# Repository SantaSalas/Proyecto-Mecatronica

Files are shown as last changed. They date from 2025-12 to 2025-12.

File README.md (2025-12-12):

<h1> Robot balancín, ¡Bienvenidos al Himalaya! </h1>

## Curso
- ME4250
## Integrantes
- Consuelo Laurie
- Martín Batarce
- Santiago Salas
- Benjamín Venegas
- Francisca Suárez
## Lista de materiales 
1. 2 Motor DC
2. 2 Ruedas
3. 3 Baterias 4V
4. 1 MPU6050
5. 1 Motor driver L298N
6. 1 Placa Arduino Uno
7. 12 Pernos M3
8. 12 Tuercas M3
9. 4 Escuadras rectangulares
10. 1 Techo CAD
11. 2 Paredes CAD
12. 1 Piso 1 CAD
13. 1 Piso 2 CAD
14. 1 Base CAD
15. 18 Cables macho-macho
16. Pegamento líquido UHU
17. Carcasa Bienvenidos al Himalaya (edición limitada)
18. 1 Switch encendido/apagado
19. 1 Portapilas
20. Cinta doble faz
21. Cinta masking tape
## Diagrama de conexiones electrónicas.
IMG-20251212-WA0009

## Manual de armado 
1. Armado Chasis: Una vez impresas todas paredes y ruedas de PLA en impresora 3d, se pegan con pegamento UHU las 4 paredes exteriores. Luego pegar escuadras metálicas cercanas a las esquinas.
*Procurar la correcta orientación de las paredes al momento de pegarlas.
2. Instalación motores: En las paredes laterales instalar ambos motores DC con pernos y tuercas M3 en los agujeros existentes. Luego con pegamento UHU, pegar las ruedas a los ejes de los motores, una rueda en cada motor.
3. Armado Piso 1: Instalar Motor driver L298N y Arduino con pernos y tuercas M3 en los agujeros existentes. Pegar Portapilas en la parte inferior del piso afirmado con cinta doble faz y cinta masking tape, se instala cercano al borde delantero y procurando que esté centrado. Luego instalar pilas y pegar al portapilas el switch de encendido/apagado con cinta doble faz.
4. Armado Piso 2: Instalar MPU6050 con pernos y tuercas M3 en los agujeros existentes.
5. Cableado: Ya instalados los componentes, seguir el diagrama de conexiones para realizar las conexiones eléctricas, utilizando los cables macho-macho.
6. Montaje: Los pisos se instalan sobre los descansos de las paredes y reforzando con pegamento UHU. Finalmente colocar la carcasa, preocurando que ningún cable que apretado entre la carcasa y la estructura.

## Puesta en marcha
1. Subir el código Arduino listo para utilizar el Robot Balancín.
2. Levantar el robot y colocar únicamente la base del robot en una superficie lisa y plana (puede ser una caja).
3. Encender el robot y esperar 3 segundos a que termine el proceso de calibración.
4. Dejar el robot libre sobre una superficie plana para que comience a balancearse.
5. En caso de falla levantar el robot por la carcasa y apagar el switch, no agarrarlo desde las ruedas.

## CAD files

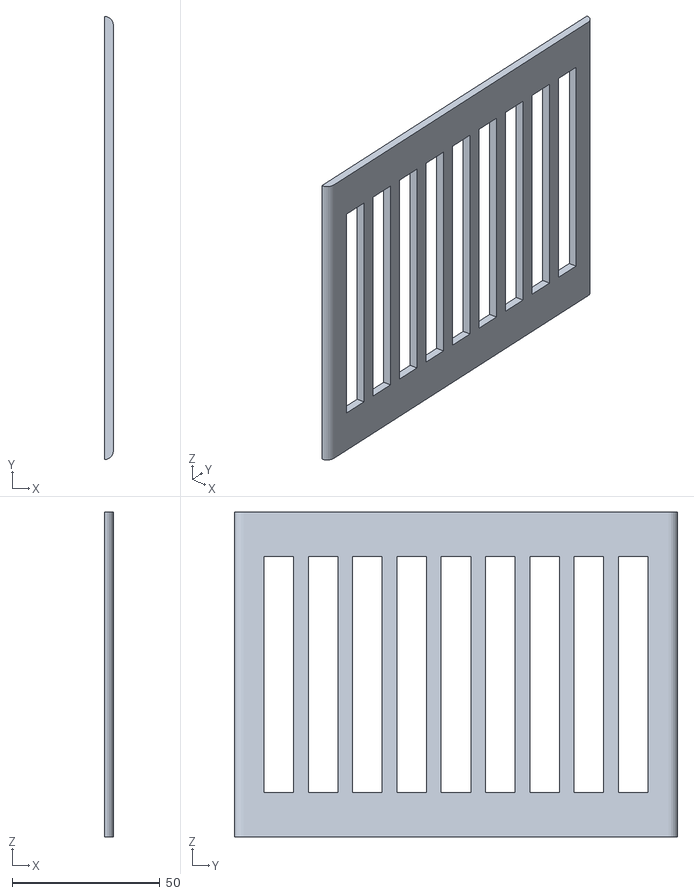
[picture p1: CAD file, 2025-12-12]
Robot Autobalacin/CAD/Techo.stl
3.00 x 150.0 x 110.0

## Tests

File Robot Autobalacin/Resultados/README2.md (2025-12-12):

## Audiovisual

WhatsApp-Image-2025-11-10-at-15 03 37-_4_
WhatsApp-Image-2025-11-10-at-15 03 37-_5_

https://github.com/user-attachments/assets/5a2925b6-6c78-46cb-873b-391fbea81871

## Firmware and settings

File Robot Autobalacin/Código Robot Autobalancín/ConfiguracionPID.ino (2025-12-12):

/*
  ROBOT AUTO-BALANCÍN - CONTROL PID COMPLETO
  ME4250 - Mecatrónica - Universidad de Chile
  Basado en estructura PID de muestra del curso
  
  Hardware: Arduino UNO + MPU6050 + L298N + 2x Motor DC
*/

#include <Wire.h>

//////////////////// CONFIGURACIÓN HARDWARE ////////////////////
// Pines MPU6050 (I2C)
const int MPU6050_ADDR = 0x68;  // Dirección I2C
// SDA -> A4, SCL -> A5 (hardware I2C)

// Pines Motor Izquierdo
const int ENA_IZQ = 5;     // PWM motor izquierdo
const int IN1_IZQ = 7;      // Control dirección
const int IN2_IZQ = 6;      // Control dirección

// Pines Motor Derecho  
const int ENB_DER = 11;     // PWM motor derecho
const int IN3_DER = 4;      // Control dirección
const int IN4_DER = 3;      // Control dirección

// Límites de seguridad
const float ANGULO_MAX = 35.0;      // [AJUSTAR] Ángulo límite seguridad
const int PWM_MIN = 50;             // [AJUSTAR] PWM mínimo efectivo
const int PWM_MAX = 255;            // PWM máximo
const int ZONA_MUERTA = 40;         // [AJUSTAR] Zona donde motores no responden

//////////////////// PARÁMETROS PID ////////////////////////////
// [AJUSTAR] Valores iniciales conservadores
float Kp = 20.0;   // Ganancia proporcional
float Ki = 0.5;    // Ganancia integral  
float Kd = 10.0;   // Ganancia derivativa
float setpoint = 0.0;  // [AJUSTAR] Ángulo objetivo (0 = vertical)

//////////////////// VARIABLES DEL CONTROL /////////////////////
float angulo = 0.0;           // Ángulo actual del robot
float error = 0.0;            // Error actual
float error_prev = 0.0;       // Error anterior
float integral = 0.0;         // Acumulador integral
float derivada = 0.0;         // Componente derivativa
float salida = 0.0;           // Salida del PID
int pwm_izq = 0;              // PWM motor izquierdo
int pwm_der = 0;              // PWM motor derecho

// Variables componentes PID (para análisis)
float P_term = 0.0;
float I_term = 0.0;
float D_term = 0.0;

// Control de tiempo
unsigned long lastTime = 0;
const unsigned long sampleTime = 10;  // [AJUSTAR] ms (100 Hz)

//////////////////// VARIABLES SENSOR MPU6050 //////////////////
// Datos crudos
int16_t accelX, accelY, accelZ;
int16_t gyroX, gyroY, gyroZ;
int16_t temperatura;

// Offsets calibración
float accelX_offset = 0;
float accelY_offset = 0;
float gyroY_offset = 0;

// Filtro complementario
const float ALPHA = 0.98;  // [AJUSTAR] 98% gyro, 2% accel

// Estado del sistema
bool sistemaCalibrado = false;
bool controlActivo = false;
bool emergencyStop = false;

//////////////////// VARIABLES ANÁLISIS MÉTRICAS ///////////////
float anguloMaximo = 0.0;     // Para calcular overshoot
float tiempoEstablecido = 0.0;  // Tiempo establecimiento
unsigned long tiempoInicio = 0;
bool primeraVez = true;
float sumaError = 0.0;         // Para error estacionario
int contadorError = 0;

//////////////////// FUNCIONES AUXILIARES - MOTORES ////////////
void configurarMotores() {
  pinMode(ENA_IZQ, OUTPUT);
  pinMode(IN1_IZQ, OUTPUT);
  pinMode(IN2_IZQ, OUTPUT);
  
  pinMode(ENB_DER, OUTPUT);
  pinMode(IN3_DER, OUTPUT);
  pinMode(IN4_DER, OUTPUT);
  
  detenerMotores();
  Serial.println("[MOTORES] Configurados OK");
}

void moverMotores(int pwmValue) {
  // Aplicar zona muerta
  if (abs(pwmValue) < ZONA_MUERTA) {
    detenerMotores();
    return;
  }
  
  // Mapear considerando zona muerta
  int pwmAjustado = abs(pwmValue);
  if (pwmAjustado > ZONA_MUERTA) {
    pwmAjustado = map(pwmAjustado, ZONA_MUERTA, PWM_MAX, PWM_MIN, PWM_MAX);
  }
  
  pwmAjustado = constrain(pwmAjustado, 0, PWM_MAX);
  
  if (pwmValue > 0) {
    // Mover adelante
    digitalWrite(IN1_IZQ, HIGH);
    digitalWrite(IN2_IZQ, LOW);
    analogWrite(ENA_IZQ, pwmAjustado);
    
    digitalWrite(IN3_DER, HIGH);
    digitalWrite(IN4_DER, LOW);
    analogWrite(ENB_DER, pwmAjustado);
    
  } else {
    // Mover atrás
    digitalWrite(IN1_IZQ, LOW);
    digitalWrite(IN2_IZQ, HIGH);
    analogWrite(ENA_IZQ, pwmAjustado);
    
    digitalWrite(IN3_DER, LOW);
    digitalWrite(IN4_DER, HIGH);
    analogWrite(ENB_DER, pwmAjustado);
  }
}

void detenerMotores() {
  digitalWrite(IN1_IZQ, LOW);
  digitalWrite(IN2_IZQ, LOW);
  analogWrite(ENA_IZQ, 0);
  
  digitalWrite(IN3_DER, LOW);
  digitalWrite(IN4_DER, LOW);
  analogWrite(ENB_DER, 0);
}

//////////////////// FUNCIONES AUXILIARES - MPU6050 ////////////
void configurarMPU6050() {
  Wire.begin();
  
  // Despertar MPU6050
  Wire.beginTransmission(MPU6050_ADDR);
  Wire.write(0x6B);  // PWR_MGMT_1
  Wire.write(0);     // Despertar
  Wire.endTransmission(true);
  
  delay(100);
  
  // Verificar comunicación
  Wire.beginTransmission(MPU6050_ADDR);
  if (Wire.endTransmission() == 0) {
    Serial.println("[MPU6050] Detectado OK");
  } else {
    Serial.println("[ERROR] MPU6050 no detectado!");
    emergencyStop = true;
  }
}

void leerMPU6050Raw() {
  Wire.beginTransmission(MPU6050_ADDR);
  Wire.write(0x3B);  // ACCEL_XOUT_H
  Wire.endTransmission(false);
  Wire.requestFrom(MPU6050_ADDR, 14, true);
  
  accelX = Wire.read() << 8 | Wire.read();
  accelY = Wire.read() << 8 | Wire.read();
  accelZ = Wire.read() << 8 | Wire.read();
  temperatura = Wire.read() << 8 | Wire.read();
  gyroX = Wire.read() << 8 | Wire.read();
  gyroY = Wire.read() << 8 | Wire.read();
  gyroZ = Wire.read() << 8 | Wire.read();
}

float calcularAngulo(float dt) {
  // Ángulo desde acelerómetro
  float accelAngulo = atan2(accelX - accelX_offset, accelZ) * 180 / PI;
  
  // Velocidad angular desde giroscopio
  float gyroRate = (gyroY / 131.0) - gyroY_offset;
  
  // Filtro complementario
  angulo = ALPHA * (angulo + gyroRate * dt) + (1 - ALPHA) * accelAngulo;
  
  return angulo;
}

void calibrarSensor() {
  Serial.println("\n[CALIBRACIÓN] Mantener robot VERTICAL y QUIETO");
  Serial.print("Calibrando");
  
  // Reset valores
  accelX_offset = 0;
  accelY_offset = 0;
  gyroY_offset = 0;
  angulo = 0;
  
  // Tomar muestras
  const int numMuestras = 200;
  long sumaAX = 0, sumaAY = 0, sumaGX = 0;
  
  for (int i = 0; i < numMuestras; i++) {
    leerMPU6050Raw();
    sumaAX += accelX;
    sumaAY += accelY;
    sumaGX += gyroX;
    
    if (i % 40 == 0) Serial.print(".");
    delay(5);
  }
  
  // Calcular offsets
  accelX_offset = sumaAX / numMuestras;
  accelY_offset = sumaAY / numMuestras;
  gyroX_offset = (sumaGX / numMuestras) / 131.0;
  
  Serial.println("\n[CALIBRACIÓN] Completada!");
  Serial.print("  Offset Gyro X: ");
  Serial.println(gyroX_offset);
  
  sistemaCalibrado = true;
  tiempoInicio = millis();
  primeraVez = true;
}

//////////////////// FUNCIÓN ANÁLISIS MÉTRICAS /////////////////
void analizarMetricas() {
  // Detectar overshoot
  if (abs(angulo) > abs(anguloMaximo)) {
    anguloMaximo = angulo;
  }
  
  // Acumular error para estacionario
  if (!primeraVez && abs(error) < 2.0) {  // Banda 2%
    sumaError += abs(error);
    contadorError++;
  }
  
  // Detectar establecimiento (criterio 2%)
  if (primeraVez && abs(error) < 1.0) {
    tiempoEstablecido = (millis() - tiempoInicio) / 1000.0;
    primeraVez = false;
    
    // Mostrar métricas
    float overshoot = abs(anguloMaximo) > abs(setpoint) ? 
                      ((anguloMaximo - setpoint) / max(abs(setpoint), 1.0)) * 100 : 0;
    
    Serial.println("\n========== MÉTRICAS PID ==========");
    Serial.print("Ts (establecimiento): ");
    Serial.print(tiempoEstablecido, 2);
    Serial.println(" seg");
    Serial.print("%OS (overshoot): ");
    Serial.print(overshoot, 1);
    Serial.println("%");
    Serial.println("==================================");
  }
}

//////////////////// SETUP //////////////////////
void setup() {
  Serial.begin(115200);
  
  Serial.println("\n  ROBOT AUTO-BALANCÍN PID V3   ");
  
  configurarMotores();
  configurarMPU6050();
  
  Serial.println("\nCOMANDOS DISPONIBLES:");
  Serial.println("  C = Calibrar sensor");
  Serial.println("  P = Iniciar control PID");
  Serial.println("  S = STOP emergencia");
  Serial.println("  + = Aumentar setpoint");
  Serial.println("  - = Reducir setpoint");
  Serial.println("  R = Reporte estado");
  Serial.println("  T = Tuning (ajuste Kp,Ki,Kd)");
  Serial.println("\nEsperando comando...\n");
  
  lastTime = millis();
}

//////////////////// LOOP PRINCIPAL //////////////////////
void loop() {
  // Procesar comandos serial
  if (Serial.available()) {
    procesarComandos();
  }
  
  // Control de emergencia
  if (emergencyStop) {
    detenerMotores();
    return;
  }
  
  // Control PID con tiempo de muestreo
  unsigned long now = millis();
  if ((now - lastTime >= sampleTime) && controlActivo && sistemaCalibrado) {
    float dt = (now - lastTime) / 1000.0;  // Convertir a segundos
    lastTime = now;
    
    // 1) Leer sensor y calcular ángulo
    leerMPU6050Raw();
    angulo = calcularAngulo(dt);
    
    // 2) Verificación de seguridad
    if (abs(angulo) > ANGULO_MAX) {
      emergencyStop = true;
      detenerMotores();
      Serial.println("[EMERGENCIA] Ángulo límite excedido!");
      return;
    }
    
    // 3) Calcular error
    error = setpoint - angulo;
    
    // 4) PID (cálculo manual como el ejemplo)
    P_term = Kp * error;
    
    integral += error * dt;
    I_term = Ki * integral;
    
    derivada = (error - error_prev) / dt;
    D_term = Kd * derivada;
    
    salida = P_term + I_term + D_term;
    
    // 5) Anti-windup (como el ejemplo)
    if (salida > PWM_MAX) {
      salida = PWM_MAX;
      integral -= error * dt;  // Evita acumulación excesiva
    } else if (salida < -PWM_MAX) {
      salida = -PWM_MAX;
      integral -= error * dt;
    }
    
    // 6) Limitar integral independientemente
    integral = constrain(integral, -100, 100);
    
    // 7) Convertir a PWM
    int pwm = (int)salida;
    
    // 8) Aplicar a motores
    moverMotores(pwm);
    
    // 9) Mostrar datos para Serial Plotter
    // Formato: angulo,setpoint,pwm,P,I,D
    Serial.print(angulo);
    Serial.print(",");
    Serial.print(setpoint);
    Serial.print(",");
    Serial.print(pwm/10.0);  // Escalar PWM para visualización
    Serial.print(",");
    Serial.print(P_term);
    Serial.print(",");
    Serial.print(I_term);
    Serial.print(",");
    Serial.println(D_term);
    
    // 10) Analizar métricas
    analizarMetricas();
    
    // 11) Guardar error anterior
    error_prev = error;
    
    // 12) Reporte error estacionario cada 2 segundos
    static unsigned long lastReport = 0;
    if (now - lastReport > 2000 && contadorError > 0) {
      float errorProm = sumaError / contadorError;
      if (errorProm < 2.0 && !primeraVez) {
        Serial.print("[ESTACIONARIO] Error promedio: ");
        Serial.print(errorProm, 2);
        Serial.println("°");
      }
      lastReport = now;
    }
  }
}

//////////////////// PROCESAMIENTO DE COMANDOS /////////////////
void procesarComandos() {
  char cmd = Serial.read();
  
  switch(cmd) {
    case 'C':
    case 'c':
      calibrarSensor();
      break;
      
    case 'P':
    case 'p':
      if (sistemaCalibrado) {
        controlActivo = true;
        emergencyStop = false;
        integral = 0;  // Reset integral
        error_prev = 0;
        Serial.println("[CONTROL] PID activado");
      } else {
        Serial.println("[ERROR] Calibrar primero con 'C'");
      }
      break;
      
    case 'S':
    case 's':
      emergencyStop = !emergencyStop;
      controlActivo = false;
      detenerMotores();
      if (emergencyStop) {
        Serial.println("[STOP] Emergencia activada");
      } else {
        Serial.println("[STOP] Sistema listo");
      }
      break;
      
    case '+':
      setpoint += 1.0;
      Serial.print("[SETPOINT] Nuevo: ");
      Serial.print(setpoint);
      Serial.println("°");
      break;
      
    case '-':
      setpoint -= 1.0;
      Serial.print("[SETPOINT] Nuevo: ");
      Serial.print(setpoint);
      Serial.println("°");
      break;
      
    case 'R':
    case 'r':
      Serial.println("\n===== ESTADO ACTUAL =====");
      Serial.print("Ángulo: ");
      Serial.print(angulo, 2);
      Serial.println("°");
      Serial.print("Setpoint: ");
      Serial.print(setpoint, 2);
      Serial.println("°");
      Serial.print("Error: ");
      Serial.print(error, 2);
      Serial.println("°");
      Serial.print("Kp: ");
      Serial.print(Kp);
      Serial.print(" | Ki: ");
      Serial.print(Ki);
      Serial.print(" | Kd: ");
      Serial.println(Kd);
      Serial.print("Calibrado: ");
      Serial.println(sistemaCalibrado ? "SI" : "NO");
      Serial.print("Control activo: ");
      Serial.println(controlActivo ? "SI" : "NO");
      Serial.println("========================");
      break;
      
    case 'T':
    case 't':
      menuTuning();
      break;
      
    case '?':
      Serial.println("\n=== AYUDA COMANDOS ===");
      Serial.println("C = Calibrar (hacer primero)");
      Serial.println("P = Activar PID");
      Serial.println("S = Stop/Resume");
      Serial.println("+/- = Ajustar setpoint");
      Serial.println("R = Reporte estado");
      Serial.println("T = Tuning PID");
      Serial.println("======================");
      break;
  }
}

//////////////////// MENÚ TUNING INTERACTIVO //////////////////
void menuTuning() {
  Serial.println("\n=== TUNING PID ===");
  Serial.println("Valores actuales:");
  Serial.print("  Kp=");
  Serial.print(Kp);
  Serial.print(" Ki=");
  Serial.print(Ki);
  Serial.print(" Kd=");
  Serial.println(Kd);
  
  Serial.println("\nIngrese nuevos valores:");
  Serial.println("Formato: P20.5 (para Kp=20.5)");
  Serial.println("         I0.8  (para Ki=0.8)");
  Serial.println("         D12.0 (para Kd=12.0)");
  Serial.println("         X     (salir)");
  
  while(true) {
    if (Serial.available()) {
      char tipo = Serial.read();
      if (tipo == 'X' || tipo == 'x') {
        Serial.println("Tuning finalizado");
        break;
      }
      
      float valor = Serial.parseFloat();
      
      switch(tipo) {
        case 'P':
        case 'p':
          Kp = valor;
          Serial.print("Nuevo Kp = ");
          Serial.println(Kp);
          break;
          
        case 'I':
        case 'i':
          Ki = valor;
          integral = 0;  // Reset integral al cambiar Ki
          Serial.print("Nuevo Ki = ");
          Serial.println(Ki);
          break;
          
        case 'D':
        case 'd':
          Kd = valor;
          Serial.print("Nuevo Kd = ");
          Serial.println(Kd);
          break;
      }
    }
  }
  
  Serial.println("\nValores finales:");
  Serial.print("  Kp=");
  Serial.print(Kp);
  Serial.print(" Ki=");
  Serial.print(Ki);
  Serial.print(" Kd=");
  Serial.println(Kd);
}

/*
  =====================================================
  GUÍA RÁPIDA DE AJUSTE PID - MÉTODO ZIEGLER-NICHOLS
  =====================================================
  
  1. AJUSTE INICIAL (Solo P):
     - Poner Ki=0, Kd=0
     - Aumentar Kp hasta oscilación sostenida
     - Anotar: Kp_critico y T_critico (periodo)
  
  2. CÁLCULO PID:
     - Kp = 0.6 * Kp_critico
     - Ki = 2 * Kp / T_critico
     - Kd = Kp * T_critico / 8
  
  3. AJUSTE FINO:
     - Si oscila: reducir Kp, aumentar Kd
     - Si lento: aumentar Kp
     - Si error permanente: aumentar Ki
  
  =====================================================
  VALORES TÍPICOS PARA ROBOT BALANCÍN
  =====================================================
  
  Robot ligero (<500g):
    Kp: 15-25
    Ki: 0.5-1.5
    Kd: 8-12
    
  Robot pesado (>500g):
    Kp: 25-40
    Ki: 1.0-2.5
    Kd: 12-20
  
  =====================================================
  SERIAL PLOTTER
  =====================================================
  
  Abrir Tools -> Serial Plotter (115200 baud)
  Se mostrarán 6 señales:
  1. Ángulo (azul)
  2. Setpoint (rojo)
  3. PWM/10 (verde)
  4. Término P (amarillo)
  5. Término I (cyan)
  6. Término D (magenta)
  
  =====================================================
*/

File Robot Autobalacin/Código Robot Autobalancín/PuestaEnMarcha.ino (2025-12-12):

#include <Wire.h>

//////////////////// CONFIGURACIÓN HARDWARE ////////////////////
const int MPU6050_ADDR = 0x68;
const int ENA = 5;         // PWM motor izquierdo
const int IN1 = 7;         // Motor izquierdo dirección
const int IN2 = 6;         // Motor izquierdo dirección  
const int ENB = 11;        // PWM motor derecho
const int IN3 = 4;         // Motor derecho dirección
const int IN4 = 3;         // Motor derecho dirección

//////////////////// PARÁMETROS PID ////////////////////////////
float Kp = 23;              // 
float Ki = 1;              // 
float Kd = 9;              // 
float setpoint = 0.0;      // Ángulo objetivo

//////////////////// PARÁMETROS SISTEMA ////////////////////////
const float ALPHA = 0.98;           // Filtro complementario
const int ZONA_MUERTA = 40;        // PWM donde motores no responden
const int PWM_MIN = 50;             // PWM mínimo efectivo
const int PWM_MAX = 255;           // PWM máximo
const float ANGULO_LIMITE = 45.0;  // Ángulo de seguridad

//////////////////// VARIABLES GLOBALES ////////////////////////
float angulo = 0.0;
float error = 0.0;
float error_prev = 0.0;
float integral = 0.0;
float derivada = 0.0;
float salida = 0.0;

unsigned long lastTime = 0;
const unsigned long sampleTime = 10;  // Control a 100Hz

int16_t accelX, accelY, accelZ;
int16_t gyroX, gyroY, gyroZ;
float gyroY_offset = 0;

bool calibrado = false;
unsigned long tiempoInicio = 0;

//////////////////// SETUP //////////////////////
void setup() {
  // Configurar pines motores
  pinMode(ENA, OUTPUT);
  pinMode(IN1, OUTPUT);
  pinMode(IN2, OUTPUT);
  pinMode(ENB, OUTPUT);
  pinMode(IN3, OUTPUT);
  pinMode(IN4, OUTPUT);
  
  // Asegurar motores detenidos
  detenerMotores();
  
  // Configurar MPU6050
  Wire.begin();
  Wire.beginTransmission(MPU6050_ADDR);
  Wire.write(0x6B);  // PWR_MGMT_1
  Wire.write(0);     // Despertar sensor
  Wire.endTransmission(true);
  
  // Esperar estabilización del sensor
  delay(500);
  
  // Calibración automática (3 segundos)
  calibrarSensor();
  
  // Inicializar tiempo
  lastTime = millis();
  tiempoInicio = millis();
}

//////////////////// LOOP PRINCIPAL //////////////////////
void loop() {
  unsigned long now = millis();
  
  // Control PID a 100Hz
  if(now - lastTime >= sampleTime) {
    float dt = (now - lastTime) / 1000.0;
    lastTime = now;
    
    // 1) Leer sensor y calcular ángulo
    leerSensor();
    calcularAngulo(dt);
    
    // 2) Verificar límite de seguridad
    if(abs(angulo) > ANGULO_LIMITE) {
      detenerMotores();
      delay(100);
      return;
    }
    
    // 3) Calcular error
    error = setpoint - angulo;
    
    // 4) Cálculo PID
    float P = Kp * error;
    
    integral += error * dt;
    float I = Ki * integral;
    
    derivada = (error - error_prev) / dt;
    float D = Kd * derivada;
    
    salida = P + I + D;
    
    // 5) Anti-windup
    if(salida > PWM_MAX) {
      salida = PWM_MAX;
      integral -= error * dt;
    } else if(salida < -PWM_MAX) {
      salida = -PWM_MAX;
      integral -= error * dt;
    }
    
    // Limitar integral
    integral = constrain(integral, -100, 100);
    
    // 6) Aplicar a motores
    int pwm = (int)salida;
    controlarMotores(pwm);
    
    // 7) Guardar error anterior
    error_prev = error;
  }
}

//////////////////// FUNCIONES AUXILIARES //////////////////////

void calibrarSensor() {
  // Calibración silenciosa (sin Serial)
  gyroY_offset = 0;
  long sumaGyroY = 0;
  long sumaAccelX = 0;
  const int numMuestras = 100;
  
  for(int i = 0; i < numMuestras; i++) {
    Wire.beginTransmission(MPU6050_ADDR);
    Wire.write(0x3B);
    Wire.endTransmission(false);
    Wire.requestFrom(MPU6050_ADDR, 14, true);
    
    accelX = Wire.read() << 8 | Wire.read();
    accelY = Wire.read() << 8 | Wire.read();
    accelZ = Wire.read() << 8 | Wire.read();
    int16_t temp = Wire.read() << 8 | Wire.read();
    gyroX = Wire.read() << 8 | Wire.read();
    gyroY = Wire.read() << 8 | Wire.read();
    gyroZ = Wire.read() << 8 | Wire.read();
    
    sumaGyroY += gyroY;
    sumaAccelX += accelX;
    
    delay(30);  // Total ~3 segundos de calibración
  }
  
  gyroY_offset = (sumaGyroY / numMuestras) / 131.0;
  
  // Calcular ángulo inicial (por si no está perfectamente horizontal)
  float accelX_prom = sumaAccelX / numMuestras;
  angulo = atan2(accelX_prom, accelZ) * 180.0 / PI;
  
  calibrado = true;
}

void leerSensor() {
  Wire.beginTransmission(MPU6050_ADDR);
  Wire.write(0x3B);
  Wire.endTransmission(false);
  Wire.requestFrom(MPU6050_ADDR, 14, true);
  
  accelX = Wire.read() << 8 | Wire.read();
  accelY = Wire.read() << 8 | Wire.read();
  accelZ = Wire.read() << 8 | Wire.read();
  int16_t temp = Wire.read() << 8 | Wire.read();
  gyroX = Wire.read() << 8 | Wire.read();
  gyroY = Wire.read() << 8 | Wire.read();
  gyroZ = Wire.read() << 8 | Wire.read();
}

void calcularAngulo(float dt) {
  // Ángulo desde acelerómetro
  float accelAngulo = -atan2(accelX, accelZ) * 180.0 / PI;
  
  // Velocidad angular desde giroscopio
  float gyroRate = (gyroY / 131.0) - gyroY_offset;
  
  // Filtro complementario
  angulo = ALPHA * (angulo + gyroRate * dt) + (1 - ALPHA) * accelAngulo;
}

void controlarMotores(int velocidad) {
  // Zona muerta
  if(abs(velocidad) < ZONA_MUERTA) {
    detenerMotores();
    return;
  }
  
  // Mapear saltando zona muerta
  int vel = abs(velocidad);
  if(vel > ZONA_MUERTA) {
    vel = map(vel, ZONA_MUERTA, PWM_MAX, PWM_MIN, PWM_MAX);
  }
  vel = constrain(vel, 0, PWM_MAX);
  
  if(velocidad > 0) {
    // Inclinado adelante -> mover adelante
    digitalWrite(IN1, HIGH);
    digitalWrite(IN2, LOW);
    analogWrite(ENA, vel);
    
    digitalWrite(IN3, HIGH);
    digitalWrite(IN4, LOW);
    analogWrite(ENB, vel);
  } else {
    // Inclinado atrás -> mover atrás
    digitalWrite(IN1, LOW);
    digitalWrite(IN2, HIGH);
    analogWrite(ENA, vel);
    
    digitalWrite(IN3, LOW);
    digitalWrite(IN4, HIGH);
    analogWrite(ENB, vel);
  }
}

void detenerMotores() {
  digitalWrite(IN1, LOW);
  digitalWrite(IN2, LOW);
  analogWrite(ENA, 0);
  
  digitalWrite(IN3, LOW);
  digitalWrite(IN4, LOW);
  analogWrite(ENB, 0);
}

/*
  ============================================
         INSTRUCCIONES DE USO FINAL
  ============================================
     - Colocar robot HORIZONTAL
     - Encender con switch
     - Esperar 3 segundos (calibración)
     - Robot se balancea automáticamente
  ============================================
*/
